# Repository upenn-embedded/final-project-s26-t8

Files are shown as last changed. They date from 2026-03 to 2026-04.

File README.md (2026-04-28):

# Final Project

**Team Number: 8**

**Team Name: Team Integr8!**

| Team Member Name | Email Address |
|---|---|
| Anjali Kalanidhi | [anjk@seas.upenn.edu](anjk@seas.upenn.edu) |
| Nevan Sujit | [tsnevan@seas.upenn.edu](tsnevan@seas.upenn.edu) |
| Sebastian William Thomann Studholme | [sthomann@seas.upenn.edu](sthomann@seas.upenn.edu) |

**GitHub Repository URL:** [https://github.com/upenn-embedded/final-project-s26-t8](https://github.com/upenn-embedded/final-project-s26-t8)

**GitHub Pages Website URL:** [https://upenn-embedded.github.io/final-project-s26-t8](https://upenn-embedded.github.io/final-project-s26-t8)

## Final Report

### 1. Video
[Demo Video](https://drive.google.com/file/d/12qTbpiO4q7P5VMjvONtVcq4hgPGpp3es/view?usp=sharing)
### 2. Images
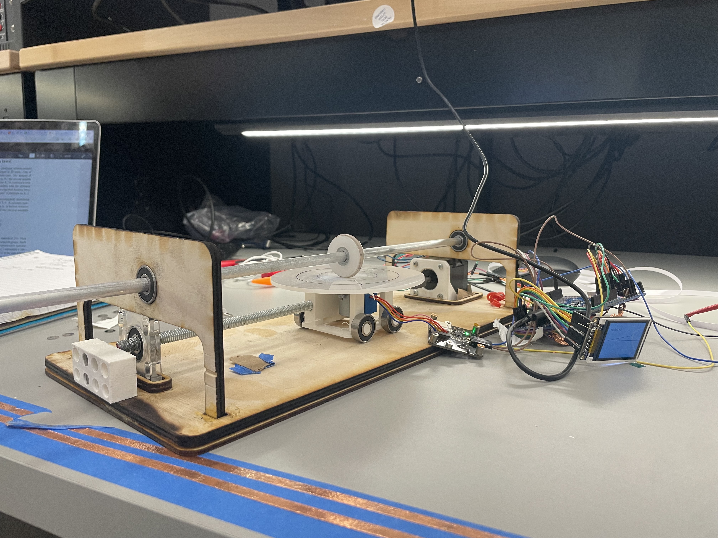
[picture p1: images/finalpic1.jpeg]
final project pictures

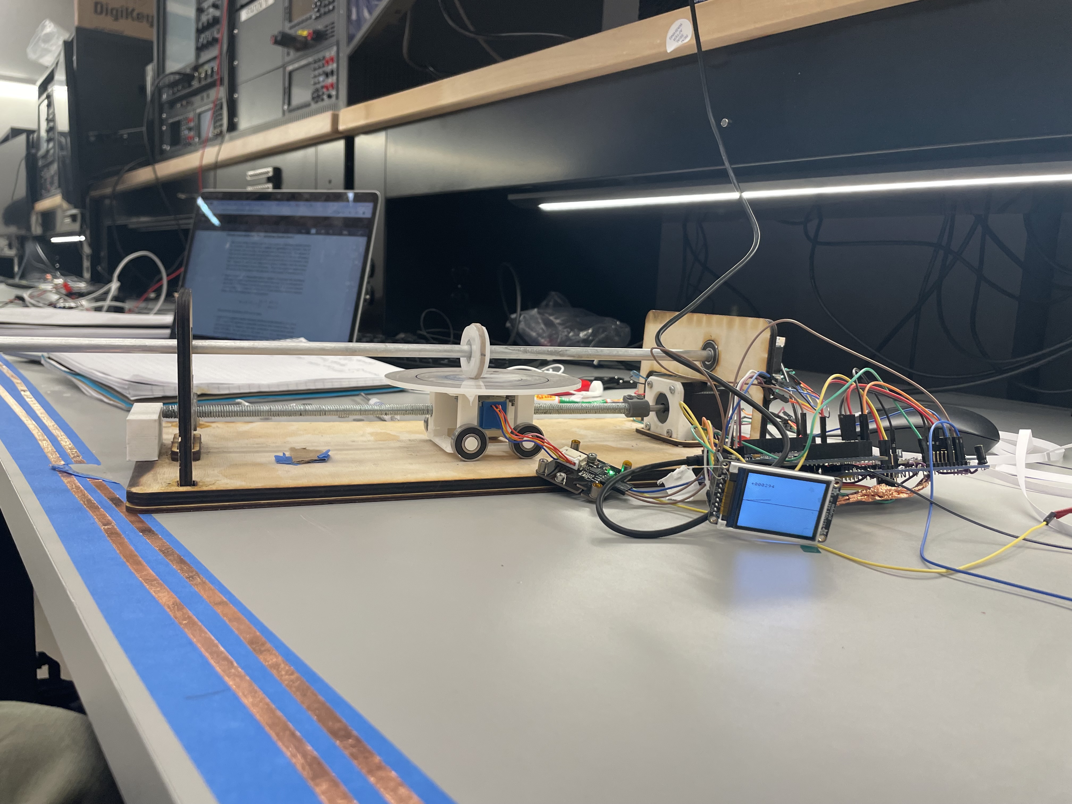
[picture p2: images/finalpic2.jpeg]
final project pictures

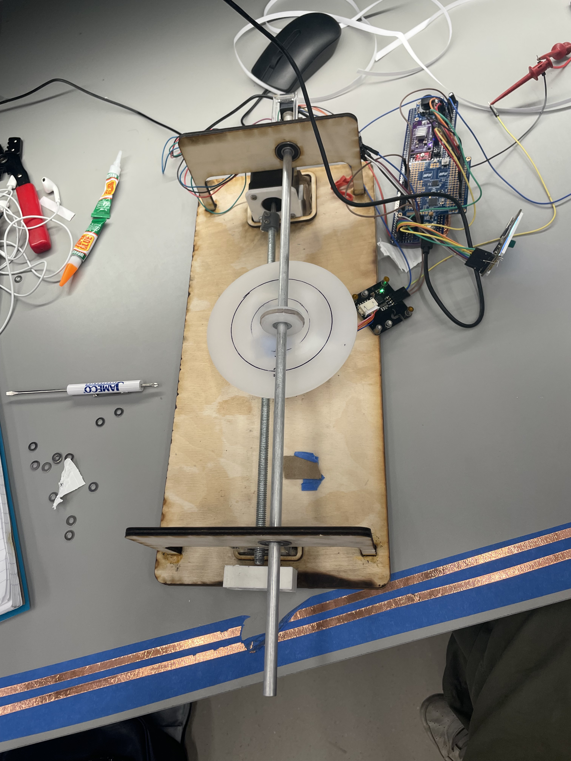
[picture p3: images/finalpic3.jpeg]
final project pictures

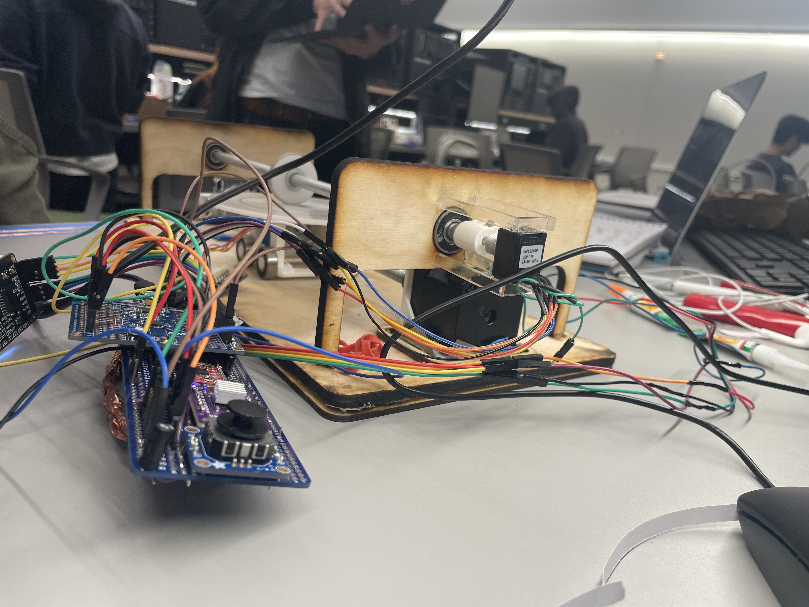
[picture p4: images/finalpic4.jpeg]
final project pictures

### 3. Results
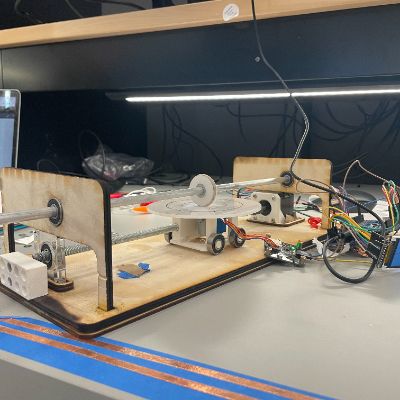
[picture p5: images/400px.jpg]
400x400 pixel picture

#### 3.1 Software Requirements Specification (SRS) Results

| ID | Description | Validation Outcome |
| --- | --- | --- |
| PWM Control | The system will generate PWM signals from the microcontroller to control motor speeds smoothly and efficiently. | Confirmed, the PWM outputs were checked via print statements and by reading an oscilloscope of the output. We had some hardware issues with this aspect, but the software worked very well. We had two different stepper motors with two different stepper motor drivers, so we had to specifically tune each code to work for each stepper motor driver, and then test and validate the PWM output coming out of each driver.  |
| Analog Input Processing | The system will read and process analog signals from the potentiometer using the onboard ADC to determine input magnitude. | We decided to use a joystick rather than a potentiometer because we felt the fact that it allowed the user to move the chassis in real time instead of simply picking a location for the chassis to end up at improved the user experience so it was easier for them to better determine which exact spot the chassis ended up at. Using the joystick also let us include variable speeds depending on how far the joystick was pushed. This system worked correctly, as we were able to check via print statements that showed us the numerical value the system was translating this input to PWM. [Joystick validation video](https://drive.google.com/file/d/1wSfRTC4DVXIuV_PTdif2x-fq1UrPfHCL/view?usp=sharing) |
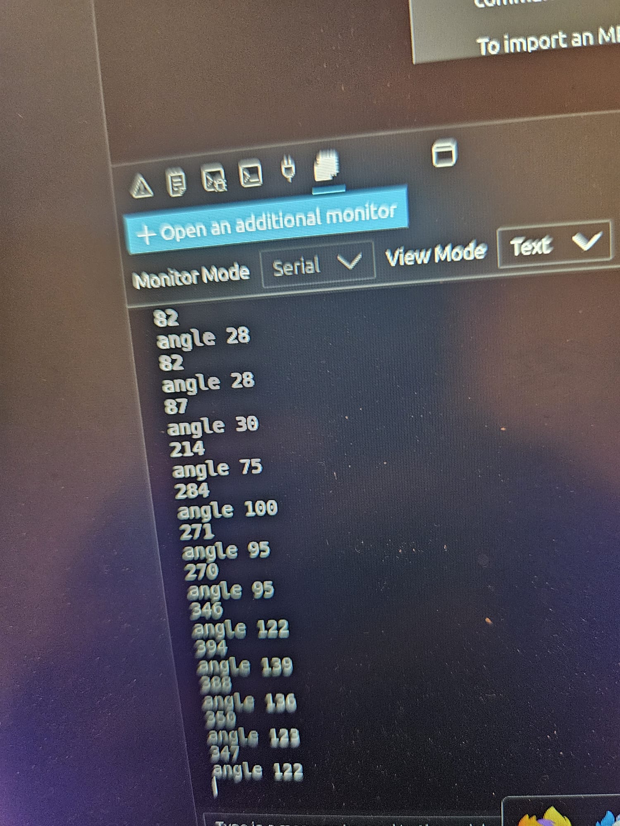
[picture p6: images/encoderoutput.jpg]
encoder validation
| Encoder Processing | The system will decode signals from the rotary encoder to track position and direction. | Works very well, we were able to confirm this is working accurately by manually measuring an angle and then using the rotary encoder and follower wheel to see if the same value is generated via print statements |
| Integration Computation | The system will keep track of rotary encoder input and sum values to calculate integral | Works well, we used print statements to see how the software sums up the positions over time, We estimate there is an error of up to 10% just by accounting for the inaccuracies of the wheel size and other mechanical limitations, but the software does its job properly. |
| Stepper Control Logic | The system will generate step and direction signals to control the stepper motor position based on the input function | We printed the out the supposed location of the stepper motor and then manually checked how far the stepper motor moved the chassis to determine if the signals were correct. This process required some tuning. |
| DC Motor Control Logic | The system will adjust DC motor speed and direction using PWM signals to maintain consistent disk rotation. | Works very well, we checked that the correct PWM signal was being generated by the software via an oscilloscope|
| Timing Control | The system will use hardware timers to maintain a fixed sampling rate for integration and motor updates. | First, we attempted to use RTOS to schedule all of the tasks needed to make this system functional. However, we ran into issues with memory space on the ATMega, so we had to switch to using ISR's instead. This ISR system works by having a hardware timer (Timer1 in CTC mode) generate an interrupt at a fixed rate of about 60 Hz, and this ISR acts as the high-priority control loop. Inside the ISR, the program reads the encoder, updates the running integral, samples the ADC, and adjusts the motor PWM and direction, ensuring these operations execute consistently. Meanwhile, the main loop runs independently as a low-priority task, handling slower operations like updating the LCD display and formatting output, even though it includes blocking delays. We ensured that this system worked by looking at an oscilloscope to see which task was happening when periodically.  |
| Display Software | The system will update the LCD via I2C to display input values, output values, and system status in real time. | Works well, we were simply able to validate this system works by checking the screen and ensuring that what we wanted to show up on the screen was actually showing up. Earlier on, we ran into some issues where the screen was not updating properly, or would turn blank after a certain amount of time, but we realized this was because the system did not have enough time to properly initialize, so by adding delays into our code, we were able to fix this issue. |

#### 3.2 Hardware Requirements Specification (HRS) Results

| ID | Description | Validation Outcome |
| --- | --- | --- |
| Power Supply Hardware | The system should include a 9 V battery and a buck converter to provide a stable 5 V supply to all electronic components. | We were unable to meet this requirement due to changes in the power requirments for the system. We initially thought our stepper motors would require 9V, but the more heavy Nema 17 motor required 24V. As a result, we were not able to order a 24V power supply in time for the demo, so we used the voltage supply for all voltages needed |
| User Input Hardware | The system should include a slider potentiometer that allows the user to manually define the input to the integrator. |Works well, we were able to check what the input is by measuring the distance the chassis moves. Our input is through a joystick instead of potentiometer, and the input signal is also relative to the maximum y values we set (the range being -2 to 2 for the final product of this project), so there were some limitations with how accurate this input could be based on what function the user actually wishes to input, but that is more of a matter of mechanical limitations rather than hardware issues. |
| Disk Rotation | There will be a DC motor-driven rotating plate mechanism that rotates at constant speed to represent time | The disk rotation was quite easy to accomplish and validate, as we were able to use an oscilloscope to see the PWM signal, and then manually count how long it takes the disk to complete a rotation to ensure that the motor driver and motor were working properly. We ended up changing this motor from a DC motor driver to a stepper motor, as that allowed us to rotate the plate at a constant speed more easily within the software stack |
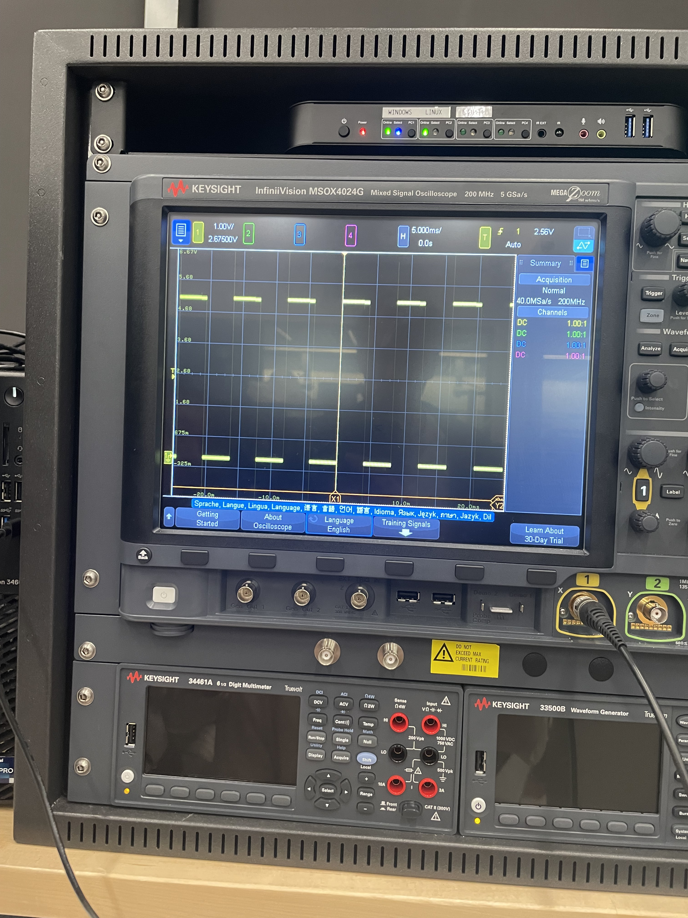
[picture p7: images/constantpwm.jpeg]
constant pwm
| DC Motor Driver | The system will include a motor driver to control the speed of the DC motor using PWM signals. | We had a lot of issues with this motor driver, as the driver fried twice. The first time, we swapped out the driver and the second time, we unsoldered and resoldered a new chip onto the motor driver, fixing these issues. We think this issue was caused by abruptly giving the motor driver power and turning it off when testing. Similar to the requirement above, we were able to validate that the output of this motor driver was correct with an oscilloscope, and this aspect of the project worked very well. Below is the PWM output for the constant plate stepper motor:  |
| Stepper motor function input | There will be a stepper motor-driven mechanism that adjusts the location of the chassis based on the input function | For the most part, this system works quite well. However, in the beginning we ran into many issues with the stepper motor stalling when we gave it power, and we spent a lot of time debugging that issue. Eventually, we realized it was due in part to torque issues caused by the clamp connecting the motor to the rod it was supposed to be turning, so we loosened the rod and attached it with glue (it could be unglued as well after use!). |
| Stepper Motor Driver | The system will include a stepper motor driver to provide precise position control via step and direction signals from the microcontroller. | We had some issues with this stepper motor beause we realized the current limit for the motor driver was set too low, causing the Nema-17 motor to stall. By increasing the potentiometer on the driver, we were able to fix this problem. This system worked pretty well, though we estimated there was likely a 10% error due to mechanical issues that happened within the system after the stepper motor driver supplied the PWM signal to the motor. We checked that the correct signal was being supplied via an oscilloscope [Stepper motor driver validation](https://drive.google.com/file/d/1TqjuBm9TQkSATUtn5irRsQ1cWkJYZEgd/view?usp=sharing) |
| Output Shaft Sensing | The system will include a rotary encoder mechanically coupled to the output shaft so that shaft rotation can be measured electronically. | Using the rotary encoder worked very well, especially once we were able to solder the pins properly. We had a few mechanical issues with placing the rotary encoder so it did not move, but overall through testing and mechanical tuning we were able to ensure this process works well through print statements. |
| Display Hardware | The system will have an LCD display connected through I2C to present system information to the user during operation. | We were able to get this system working well so that it displays the integral function as well as the value of the integral. We originally had some overflow issues with the display, causing it to blank out, but by switching from an RTOS system to one dirven by ISR's and adding in proper delays for startup, we were able to fix this problem. |

### 4. Conclusion
Overall, we found this project to be immensly fulfilling and each felt that our we gained very valuable skills not only in embeded C, but in learning how to plan and put a whole project together, learning which parts to pick and what to account for when picking parts, and how to CAD, laser cut, and understand how to integrate software, electrical, and mechanical parts together to make a complete project. 

Some important things we learned about were knowing which software techniques to use when (RTOS may have been better at scheduling, but the memory limitations of the ATMega showed us that using ISR's was the better option). We also worked on many different parts of the code at once, and then had to integrate them all together, which allowed different members of the team to always have something to do, but led to some changes having to be made during software integration to account for the fact that different people writing code may affect the efficiency of the system. We also got good at learning how to diagnose if a problem was due to software, electrical, or mechanical components, like when our Nema 17 motor was stalling (a mix of electrical and mechanical) or when the LCD screen was not displaying properly (software). A big unexpected challenge for us was putting all the mechanical components together. We understood that this project was very mechanical-heavy, but underestimated how many clamps and chassis' would break, had a lot of trouble figuring out tolerances (tolerances for laser cutting with wood vs acrylic vs 3D printing led to a **lot** of trial and error), and didn't really account for the time it takes to lasercut/print. As a result, on the morning of our demo, the threading in our chassis that allows the Nema-17 to move the plate left and right wore down, and we were scrambling to print a new one for our demo. Overall, we felt that we met pretty much all of our software/hardware requirements, but the mechanical aspects of our project were what was holding us back from making it even more complete. Our project is a great prototype, but next time, designing with mechanical integration in mind earlier could help us a lot in minimizing error. Our next steps for this project would be to redesign our actual frame so it fits together better and to consolidate our power supplies with a buck converter so we can power the entire system with a single 24V power supply.

## References
We first learned about the mechanical integrator from a Youtube video titled [The Mechanical Integrator - a machine that does calculus](https://www.youtube.com/watch?v=s-y_lnzWQjk) by Jack Monaco. We wanted to try and build this project for ourselves, adding complexity with the LCD screen as well as user input. We emailed the author of this video to ask him for the CAD model of his design to use as a basis for ours, but found that his design was pretty underdeveloped/incomplete. Instead, we used his design as a basis to create our CAD model.

## Final Project Proposal

### 1. Abstract
A mechanical integrator is a device that physically computes the integral of a function by converting a changing input into accumulated motion over time. Historically, mechanisms like these were used in early analog computers to solve math problems before modern digital computers were available. In this project, we are building a microcontroller-assisted mechanical integrator that demonstrates this concept in an interactive way. A slider potentiometer allows the user to control a time-varying input value, which is read by an ATmega328P microcontroller. The system drives a motor that changes speed as an analog to the function value over time and the mechanical integrator uses the motor encodings to calculate the accumulated distance travelled over time, which is an analog to an integral. The microcontroller will output the behavior of the input and the resulting integral on a small LED display and on the serial plotter. 

### 2. Motivation
We are building our mechanical integrator to create a more computation-efficient way to solve integrals, particularly because the ATMega328P is not well-suited for computing complex mathematical problems. This project is interesting because we are building a mechanical integrator, a device that was historically used to calculate complex integrals, but updating it with the modern firmware capabilities of the ATMega to show that analog based technologies still have their merits.

### 3. System Block Diagram
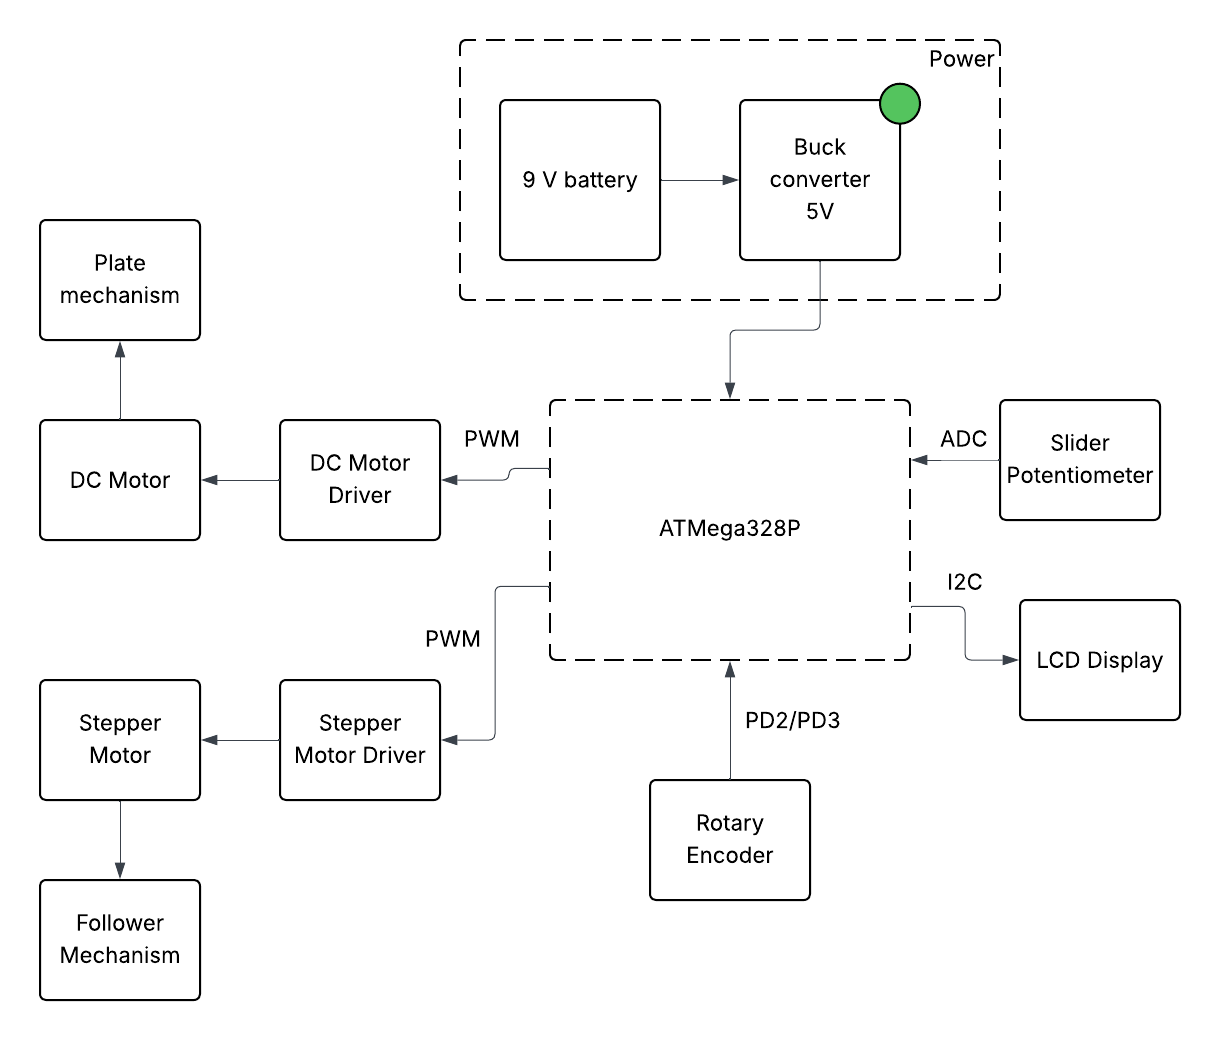
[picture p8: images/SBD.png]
System Block Diagram

### 4. Design Sketches
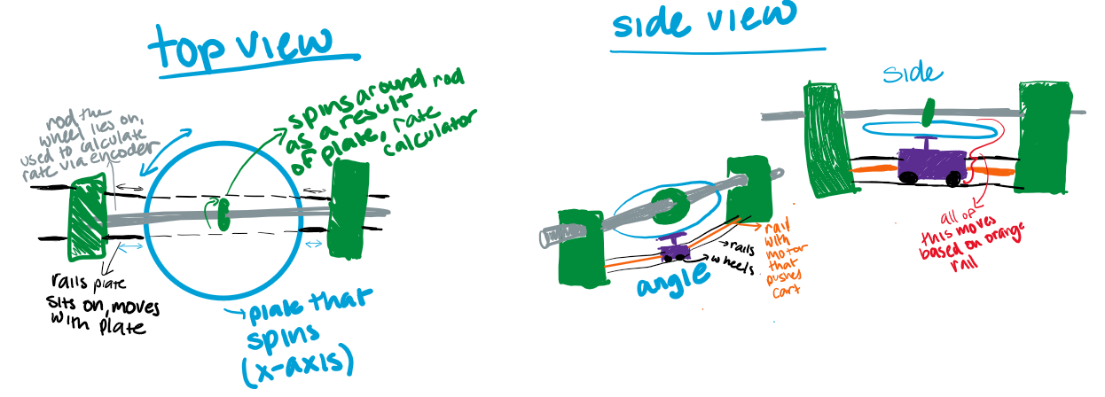
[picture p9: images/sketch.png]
Sketch

### 5. Software Requirements Specification (SRS)

**5.1 Definitions, Abbreviations**

Here, you will define any special terms, acronyms, or abbreviations you plan to use for hardware

**5.2 Functionality**

| ID | Description |
| --- | --- |
| PWM Control | The system will generate PWM signals from the microcontroller to control motor speeds smoothly and efficiently. |
| Analog Input Processing | The system will read and process analog signals from the potentiometer using the onboard ADC to determine input magnitude. |
| Encoder Processing | The system will decode signals from the rotary encoder to track position and direction. |
| Integration Computation | The system will keep track of rotary encoder input and sum values to calculate integral |
| Stepper Control Logic | The system will generate step and direction signals to control the stepper motor position based on the input function |
| DC Motor Control Logic | The system will adjust DC motor speed and direction using PWM signals to maintain consistent disk rotation. |
| Timing Control | The system will use hardware timers to maintain a fixed sampling rate for integration and motor updates. |
| Display Software | The system will update the LCD via I2C to display input values, output values, and system status in real time. |

### 6. Hardware Requirements Specification (HRS)

**6.1 Definitions, Abbreviations**

Here, you will define any special terms, acronyms, or abbreviations you plan to use for hardware
Plate: The bottom, flat, circular disk that is rotated by a motor to represent the x-axis.
Follower: the small wheel attached to a rod that spins as a result of the plate rotation

**6.2 Functionality**

| ID | Description |
| --- | --- |
| Power Supply Hardware | The system should include a 9 V battery and a buck converter to provide a stable 5 V supply to all electronic components. |
| User Input Hardware | The system should include a slider potentiometer that allows the user to manually define the input to the integrator. |
| Disk Rotation | There will be a DC motor-driven rotating plate mechanism that rotates at constant speed to represent time |
| DC Motor Driver | The system will include a motor driver to control the speed of the DC motor using PWM signals. |
| Stepper motor function input | There will be a stepper motor-driven mechanism that adjusts the location of the chassis based on the input function |
| Stepper Motor Driver | The system will include a stepper motor driver to provide precise position control via step and direction signals from the microcontroller. |
| Output Shaft Sensing | The system will include a rotary encoder mechanically coupled to the output shaft so that shaft rotation can be measured electronically. |
| Display Hardware | The system will have an LCD display connected through I2C to present system information to the user during operation. |

### 7. Bill of Materials (BOM)
A 10k slider potentiometer will serve as the primary input as it will be used as the analog for function value over time. The potentiometer will be connected to an ADC pin on the microcontroller so that the system can read the input value.

The mechanical integrator requires two motors. A DC gear motor will rotate the time disk, providing the constant motion needed for the integration process. This motor will be controlled using a motor driver, which allows the microcontroller to regulate motor speed using PWM signals. A stepper motor will be used to control the position of the follower mechanism. A stepper motor is needed here as we need precise position control and it will be driven using an EasyDriver stepper motor driver.

To measure the output of the integrator, a rotary encoder will be attached to the output shaft. The encoder will generate pulses that the microcontroller can count using interrupt pins to determine how much the shaft has rotated.

Finally, an LCD display will be used to display the integral value. The display will communicate with the microcontroller using the I2C interface and will show information such as the input value and the integrated output.

[BOM](https://docs.google.com/spreadsheets/d/1b2L2CsoX9tYtY7pSSJdgno0QYMjl8iTiAHsGNdwpyRs/edit?usp=sharing)

### 8. Final Demo Goals
On demo day, the device will be demonstrated on tabletop. A user will control the input function using the slider potentiometer, which changes the motor speed over time. As the slider is moved, the mechanical system will compute the integral through its physical motion, while the microcontroller reads and visualizes the output integral on an LED display.

During the demonstration, several simple input patterns representing basic functions will be shown, such as holding the slider at a constant value (y=c), changing it linearly over time (y=mx), and sinusoidal functions. These examples will illustrate how the output accumulates and how the integral changes based on the input. The main constraints for the demo are ensuring that the mechanical components are properly aligned and calibrated.

### 9. Sprint Planning

| Milestone  | Functionality Achieved | Distribution of Work |
| --- | --- | --- |
| Sprint #1  | Build the entire project on CAD. Since this project requires a fair amount of laser cutting + 3D printing, we want to make sure that we design all those parts before we design anything physically. Not only should the entire design, including the manufactured parts and electrical components be in our CAD design, but we also want to create simulations in our design for how the mechanisms should move.  | Anjali CAD's the plate & things it is connected to, Nevan CAD's the follower and things it is connected to, Sebastian CAD's all integration |
| Sprint #2  | Following this our second milestone will be to both print and assemble the manufactured parts with the electrical components, and then program the MCU to take in the potentiometer input and output the correct PWM signals and take the motor’s encodings to calculate the integral. With these two milestones, we will have essentially finished building our project. | Anjali handles printing of parts and mechanical side of things, Sebastian works on software, Nevan works on electronics. Everyone is working together to integrate, so tasks are not as clear cut |
| MVP Demo | Potentiometer input leads to function displayed through serial monitor, integral output, as well as LCD showing the integral numerical value. | Anjali works further on mechanical/software integration, Sebastian and Nevan finish coding. Most of this week will be spent tuning device and making sure it works well. |
| Final Demo | if time permits we want to build a way for the user to draw rather than use a potentiometer to create their function. The user would draw their desired function that they want to integrate on a display and then this drawing gets converted to a list of numbers that the MCU can then read to control the PWM signal to input into the motor. The output could then also be displayed in the serial as the distance travelled by the motor over time. | Sebastian CAD's mechanical components, Anjali and Nevan work on software/electrical updates to make new features work. |

**This is the end of the Project Proposal section. The remaining sections will be filled out based on the milestone schedule.**

## Sprint Review #1

### Last week's progress
We have CAD'd most of the model for the project and ordered all the components we need. We finalized which components we wanted to go with, including picking which motors to use and deciding which components in Detkin we can use and which components we want to order. We have finalized the CAD design for the wheel and for the connectors between the frame and the rods. We have begun laser cutting and are planning on finishing assembly physically integrate our electronic components into the design next week. We still need to figure out how to add wheels to the chassis that the plate spins on and how to connect the rotary encoder to the follower wheel and shaftf, so those will be mechanical challenges we need to figure out next week.
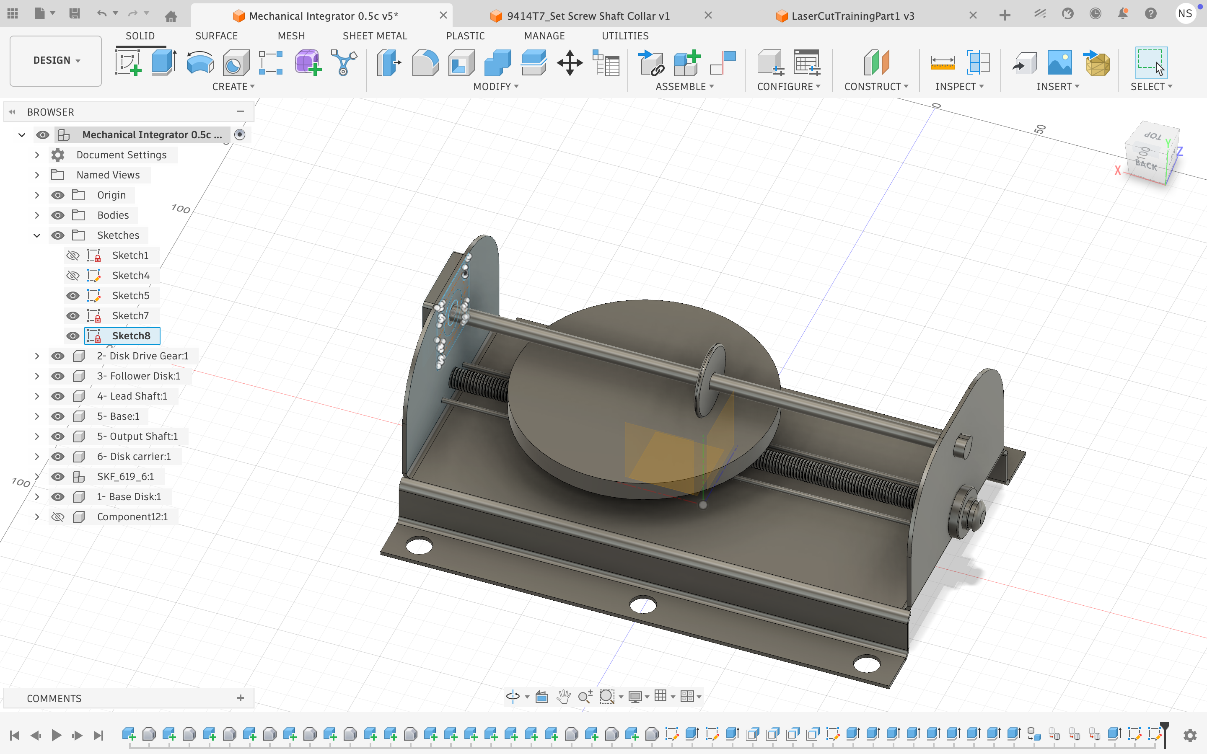
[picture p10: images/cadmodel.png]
cad model

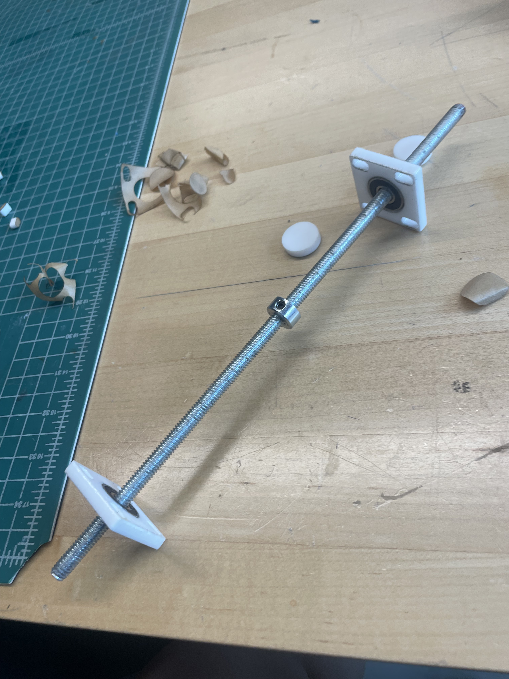
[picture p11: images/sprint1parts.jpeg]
parts we cut

### Current state of project
We have a pretty solid foundation for this project. We understand how it works mechanically, which parts should be connected to one another, and how we want to integrate electronics. We have all parts purchsed, and at this point we just need to focus on finishing the mechanical parts and assembly as soon as possible so we can focus on hardware.
### Next week's plan
Finishing printing and assembly, create a plan for how we are physically going to wire up our components, and create system diagrams for our code so we can integrate everything completely the week after.
| Assignee | Task | Estimated time | Finished when... |
| ---| -----|--- | --- |
| Nevan  | CAD and print the chassis | Two hours | The chassis is printed |
| Sebastian  | Connector between rotary encoder and follower shaft wheel | Two hours | Connector is printed and glued to rotary encoder and shaft |
| Anjali | Connect follower wheel to shaft to bearings to rotary encoder | 1 hour | Entire top piece is connected |
| Nevan | CAD and print base | Two hours | Base is printed |
| Anjali | CAD and print wheels | Two hours | Wheels are printed and connected to chassis as well as track |
| Sebastian | Final assembly | Two hours | Connect all pieces together, motors are placed in correct location |
## Sprint Review #2

### Last week's progress
We completely finished CADing and most of our parts are printed. We had to alter tolerances because we made some of them too tight, so we are currently just waiting on those last parts to print. Most of our electronics have come in as well so we have begun to write code as well as assemble. We are splitting each of the components into separate code segments and then planning on integrating all the code together. The code for the follower wheel encoder, which actually calculates the integral, is complete. 
output from encoder
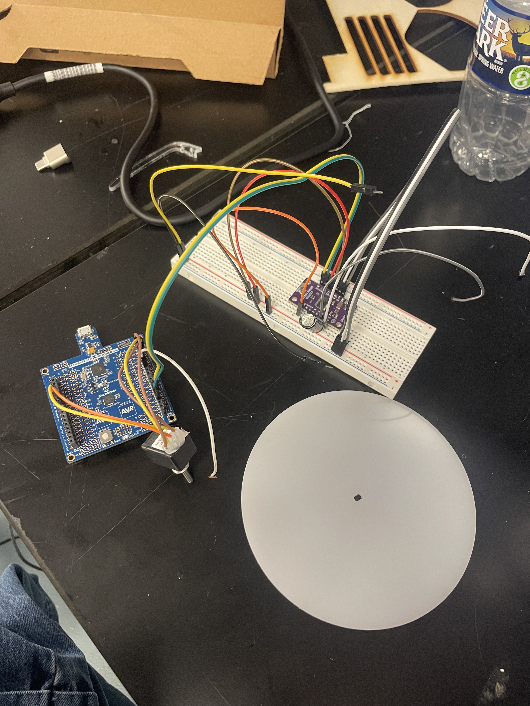
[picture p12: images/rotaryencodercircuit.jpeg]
circuit with rotary encoder

### Current state of project
We have code for the rotary encoder that tells you the correct integral value, and most of the components assembled together, we just need to add them to the frame.
### Next week's plan
Finishing coding is top priority, then working on assembly. There are lag times in getting our mechanical parts finished, but since we have the motors and drivers we need, we can work on writing code in the meantime to make integration go smoother. Because the mechanical aspect of this project is taking longer than expected, we are focusing on getting the integral to work with a manual function input, and then will add user input the following week.
| Assignee | Task | Estimated time | Finished when... |
| ---| -----|--- | --- |
| Nevan  | print the frame | one hour | The frame is printed/ made sure all componenets are correct sizes/fit |
| Sebastian  | assemble the frame | two hours | mechanical frame is fully complete with all separate components |
| Anjali | integrate electronics  | 2 hour | all electronics are in the frame |
| Nevan | code the big stepper motor/y axis | five hours | the rod moves in tandem with the y axis of a function |
| Anjali | code the time/constant plate, integrate all code together | five hours | all code is complete |
| Sebastian | final integration | five hours | Connect all pieces together, motors are placed in correct location, fully integrated together |
| Nevan | Code LCD Screen output | two hours | LCD properly displays what integral value we want it to |
## MVP Demo
[Slide deck](https://docs.google.com/presentation/d/1c26fR2l8V-HrHxDpfWXI8LoWvZEP7CJ0bPEYAke9Whs/edit?usp=sharing)

System block diagram:
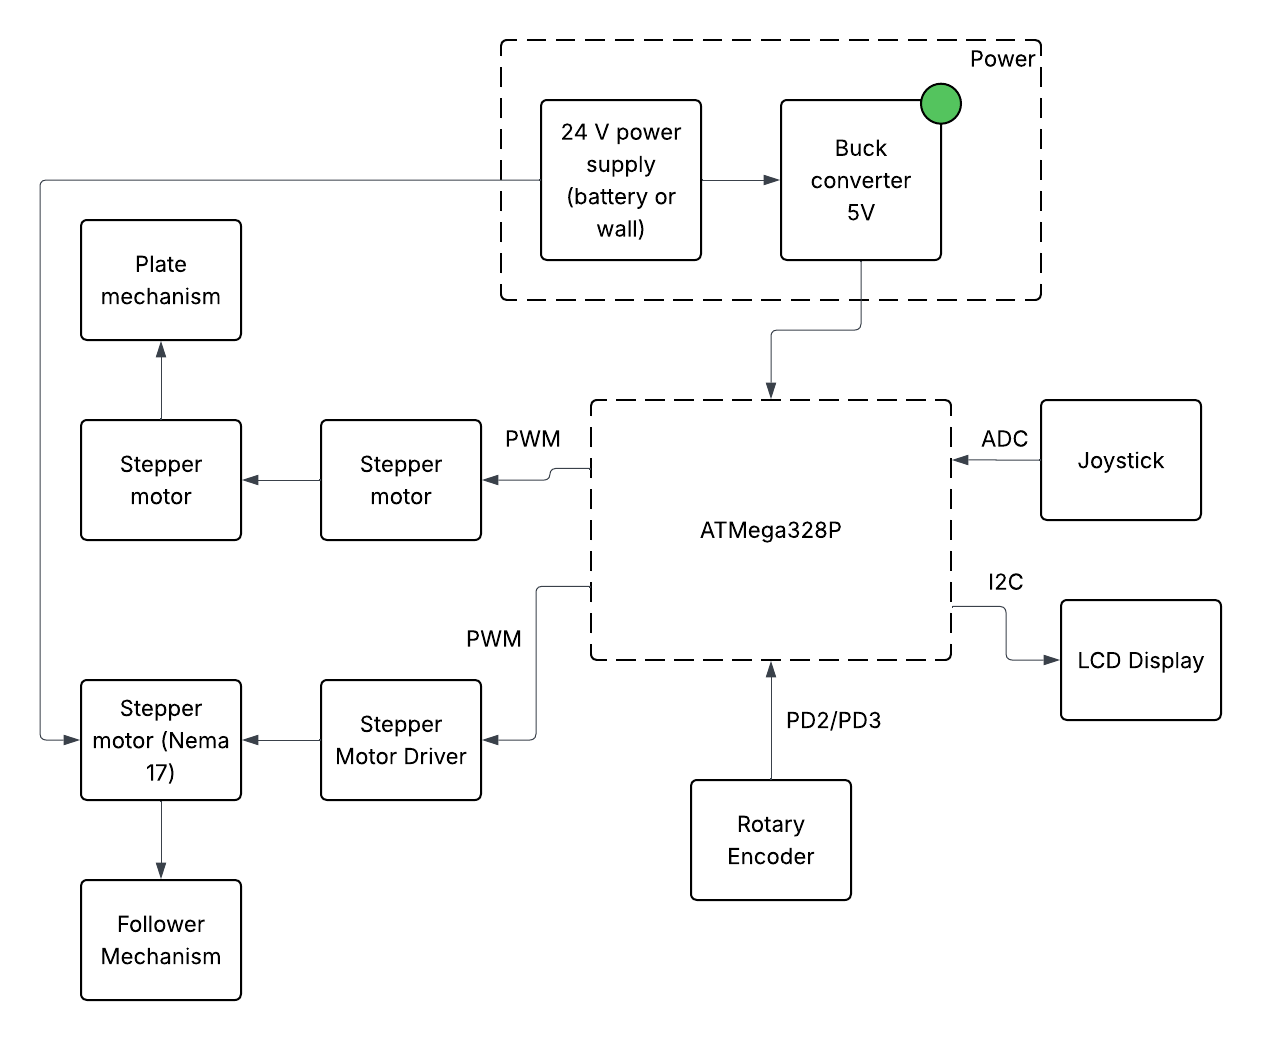
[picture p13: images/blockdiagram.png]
System block diagram


Hardware explanation:
The hardware system is organized around the ATmega328P microcontroller, which serves as the central controller coordinating power, sensing, and actuation. A 24 V power supply provides the primary energy source, which is stepped down to 5 V using a buck converter to safely power the microcontroller and low-voltage peripherals. User input is provided through a joystick connected to an ADC pin. The ATMega processes this input and turns it into PWM outputs for the motors. One stepper motor (turning the plate) establishes the time base by driving the plate mechanism, while another stepper motors (the heavy duty NEMA 17) is used to represent the y axis of the function input. This movement turns the follower wheel, which turns the rotary encoder connected to digital pins (PD2/PD3) which read the angle position. The ATMega then processes this data and sums up the overall change in angle to find the total integral. An LCD display communicates with the microcontroller over I2C, enabling real-time visualization of the integral as well as its value. The system operates in a closed-loop style at the user level: the user sets an input via the potentiometer or joystick, the microcontroller processes this input and generates appropriate control signals, the motors actuate the mechanical system, and the resulting motion is observed through the encoder feedback and displayed on the LCD.

Firmware implementation:
The firmware is structured into modular components that separately handle sensing, user interaction, and motor control while remaining tightly coordinated through the main control loop. One module manages the rotary encoder and LCD output, where interrupt-driven inputs from the encoder (on PD2/PD3) are used to track position or system output in real time, and this information is formatted and transmitted over I2C to the display for user feedback. A second module controls the NEMA 17 stepper motor responsible for the y-axis (input function), generating precise step and direction signals to map the user-defined input—set via the potentiometer or joystick—into accurate vertical motion. The third module governs the stepper motor driving the plate mechanism, which acts as the x-axis (time base) by running at a constant, calibrated speed to ensure a uniform progression of time. Together, these modules create a synchronized firmware architecture where the time axis advances steadily, the input axis responds dynamically to user control, and the system state is continuously measured and displayed, effectively implementing the mechanical integration behavior.

Software Requirements Specifications:
The software is designed to integrate sensing, computation, and actuation into a single cohesive system. Analog input processing is implemented thorugh the joystick, allowing user-defined inputs to be continuously sampled. Rotary encoder processing is tightly coupled with the integration computation, enabling real-time calculation of the system’s output within the same execution flow. While the integration logic is functional and produces correct mathematical behavior, further tuning of variables is required to improve accuracy and stability. During development, stack overflow issues were encountered, indicating memory constraints that required optimization of function usage and data handling. Stepper motor control for the input axis and time axis are both operational, though additional tuning is needed—particularly for incorporating encoder feedback to correct accumulated positional errors over time.

From a timing perspective, a structured scheduling approach through RTOS has been implemented to reliably sequence encoder reading, integration computation, and LCD updates, ensuring consistent real-time performance. However, this timing framework still needs to be extended to both stepper motors. The display system is complete, providing clear real-time feedback of system state, including input and output values. Overall, the software is functionally complete but requires further calibration and optimization, as well as full integration of all systems through RTOS.

Hardware Requirement Specifications:
The hardware implementation centers on the ATmega MCU. Power is currently supplied through multiple working sources, so distribution architecture still needs to be consolidated. User input is provided via a joystick that feeds analog signals into the MCU, where the ADC reliably converts them into digital values for processing. The rotary encoder is functioning well and provides consistent, accurate measurements, while the disk rotation mechanism for the time axis is also operating as expected. The display hardware and stepper motor driver are both stable and performing reliably within the system.

On the actuation side, stepper motor drivers are generally functional but require further tuning, particularly for the NEMA 17 motor, which is experiencing jitter and lag. These issues are mostly caused by mechanical factors such as friction, misalignment, or load inconsistencies in the mechanism. Overall, while the core hardware components are working, final performance depends on improving both driver tuning and mechanical integration to reduce lag and ensure consistent motion.

Risk mitigation:
To mitigate the risk of high voltage damaging components or overheating motors, hardware safeguards such as current limiting, proper driver configuration, and protective circuitry (e.g., fuses or thermal shutdown features) are implemented to prevent excessive power draw. Mechanical failures are addressed by reinforcing all structural components using secure fasteners like screws instead of adhesives, ensuring greater durability and stability under load. Together, these measures improve both electrical safety and mechanical reliability of the system.

Next steps:
The next steps focus on fully integrating the mechanical and control subsystems into a single cohesive system, ensuring that the firmware and hardware operate seamlessly together. Mechanically, the device will be assembled and reinforced, while the power system will be standardized to a single wall supply for simplicity and reliability. Additionally, debugging efforts will target stepper motor jittering to improve motion smoothness and overall system performance.

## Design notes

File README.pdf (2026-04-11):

README.md | 2026-04-11

# Final Project

Team Number: 8

Team Name: Integr8

Team Member Name | Email Address
Anjali Kalanidhi | anjk@seas.upenn.edu
Nevan Sujit | tsnevan@seas.upenn.edu

Sebastian William Thomann Studholme sthomann@seas.upenn.edu

GitHub Repository URL: https://github.com/upenn-embedded/final-project-s26-t8

GitHub Pages Website URL: [for final submission]*

## Final Project Proposal

1. Abstract

A mechanical integrator is a device that physically computes the integral of a function by converting a changing input into accumulated motion over time. Historically, mechanisms like these were used in early analog computers to solve math problems before modern digital computers were available. In this project, we are building a microcontroller-assisted mechanical integrator that demonstrates this concept in an interactive way. A slider potentiometer allows the user to control a time-varying input value, which is read by an ATmega328P microcontroller. The system drives a motor that changes speed as an analog to the function value over time and the mechanical integrator uses the motor encodings to calculate the accumulated distance travelled over time, which is an analog to an integral. The microcontroller will output the behavior of the input and the resulting integral on a small LED display and on the serial plotter.
2. Motivation

We are building our mechanical integrator to create a more computation-efficient way to solve integrals, particularly because the ATMega328P is not well-suited for computing complex mathematical problems. This project is interesting because we are building a mechanical integrator, a device that was historically used to calculate complex integrals, but updating it with the modern firmware capabilities of the ATMega to show that analog based technologies still have their merits.
3. System Block Diagram

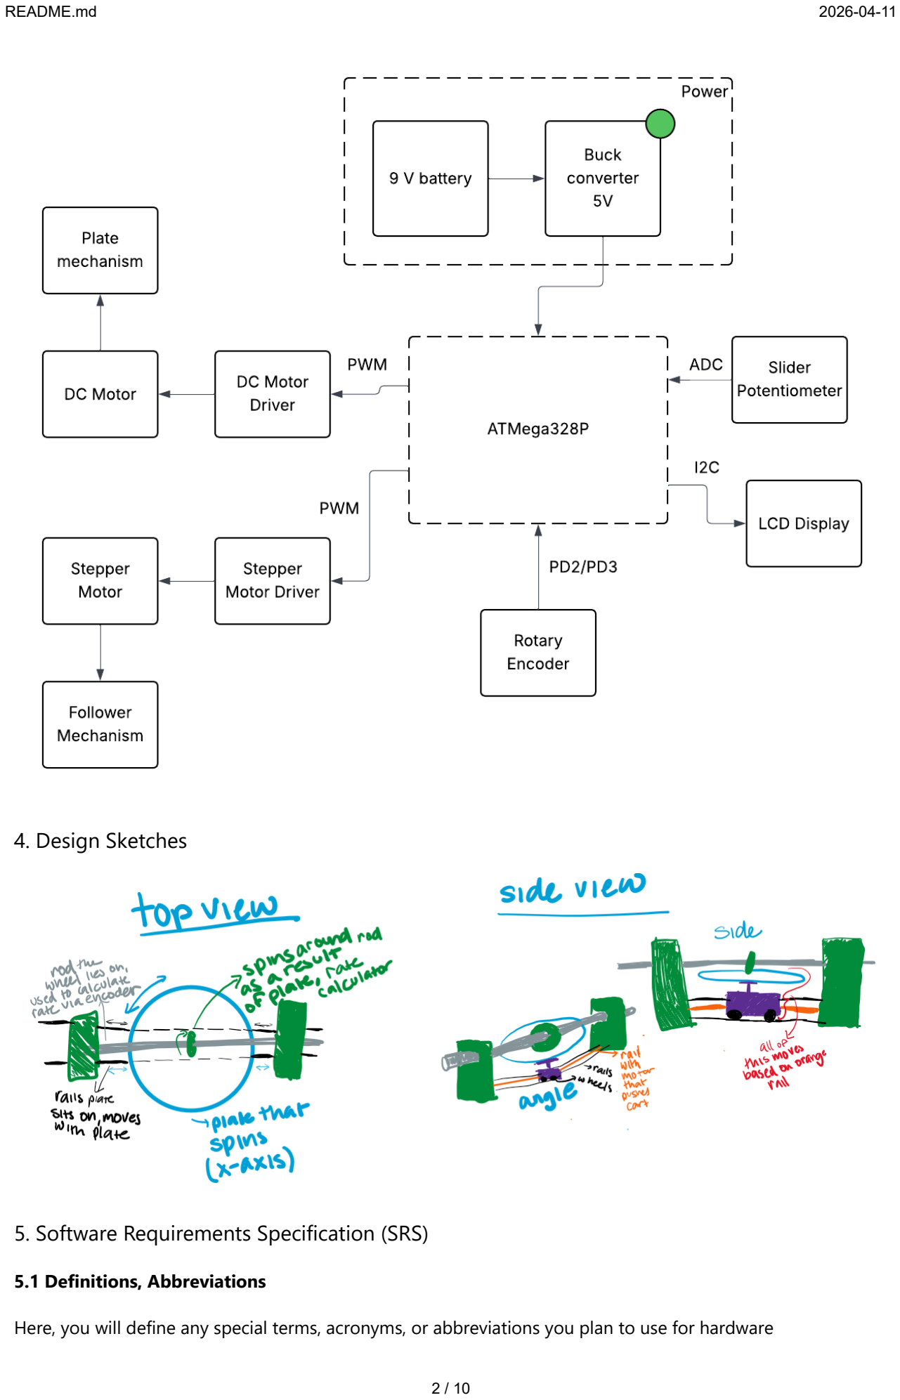
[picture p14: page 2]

4. Design Sketches
5. Software Requirements Specification (SRS)

### 5.1 Definitions, Abbreviations

Here, you will define any special terms, acronyms, or abbreviations you plan to use for hardware

### 5.2 Functionality

ID | Description
Analog Input Sampling | The IMU 3-axis acceleration will be measured with 16-bit depth every 100 milliseconds +/-10 milliseconds

Constant
Disk Motor Control | The software shall drive the disk motor at a constant speed using PWM control.

Follower
position

The software should drive the stepper motor to move the follower mechanism according to the input value from the slider potentiometer. We can test this by setting several known slider positions and checking that the follower moves to the expected corresponding positions.

Output
measurement

The software should read pulses from the rotary encoder using interrupts in order to track the output shaft rotation in real time. We’ll test this by rotating the output shaft by a known amount and checking that the encoder count changes by the expected amount.

LCD Display

The software should update the LCD display and serial plotter in real time to show the current input value and the accumulated output of the integrator.

6. Hardware Requirements Specification (HRS)

### 6.1 Definitions, Abbreviations

Here, you will define any special terms, acronyms, or abbreviations you plan to use for hardware Plate: The bottom, flat, circular disk that is rotated by a motor to represent the x-axis. Follower: the small wheel attached to a rod that spins as a result of the plate rotation

### 6.2 Functionality

ID | Description
User Input Hardware | The system should include a slider potentiometer that allows the user to manually define the input to the integrator.
Disk rotation | There will be a motor-driven rotating disk that provides the time base for the mechanical integrator.
Follower position movement | There will be a motorized follower-position mechanism that adjusts the follower location based on the user input. We will test this by making the mechanism move to multiple positions and verifying it moves to those correct positions.
Output Shaft Sensing | The system will include a rotary encoder mechanically coupled to the output shaft so that shaft rotation can be measured electronically.
Display Hardware | The system will have an LCD display connected through I2C to present system information to the user during operation.
7. Bill of Materials (BOM)

A 10k slider potentiometer will serve as the primary input as it will be used as the analog for function value over time. The potentiometer will be connected to an ADC pin on the microcontroller so that the system can read the input value.

The mechanical integrator requires two motors. A DC gear motor will rotate the time disk, providing the constant motion needed for the integration process. This motor will be controlled using a motor driver, which allows the microcontroller to regulate motor speed using PWM signals. A stepper motor will be used to control the position of the follower mechanism. A stepper motor is needed here as we need precise position control and it will be driven using an EasyDriver stepper motor driver.

To measure the output of the integrator, a rotary encoder will be attached to the output shaft. The encoder will generate pulses that the microcontroller can count using interrupt pins to determine how much the shaft has rotated.

Finally, an LCD display will be used to display the integral value. The display will communicate with the microcontroller using the I2C interface and will show information such as the input value and the integrated output.

BOM (https://docs.google.com/spreadsheets/d/1b2L2CsoX9tYtY7pSSJdgno0QYMjl8iTiAHsGNdwpyRs/edit?usp=sharing)
8. Final Demo Goals

On demo day, the device will be demonstrated on tabletop. A user will control the input function using the slider potentiometer, which changes the motor speed over time. As the slider is moved, the mechanical system will compute the integral through its physical motion, while the microcontroller reads and visualizes the output integral on an LED display.

During the demonstration, several simple input patterns representing basic functions will be shown, such as holding the slider at a constant value (y=c), changing it linearly over time (y=mx), and sinusoidal functions. These examples will illustrate how the output accumulates and how the integral changes based on the input. The main constraints for the demo are ensuring that the mechanical components are properly aligned and calibrated.
9. Sprint Planning
Milestone Functionality Achieved | Distribution of Work

Sprint #1

Build the entire project on CAD. Since this project requires a fair amount of laser cutting + 3D printing, we want to make sure that we design all those parts before we design anything physically. Not only should the entire design, including the manufactured parts and electrical components be in our CAD design, but we also want to create simulations in our design for how the mechanisms should move.

Anjali CAD's the plate &
things it is connected to, Nevan CAD's the follower
and things it is connected to, Sebastian CAD's all
integration

Milestone Functionality Achieved | Distribution of Work

Sprint #2

Following this our second milestone will be to both print and assemble the manufactured parts with the electrical components, and then program the MCU to take in the potentiometer input and output the correct PWM signals and take the motor’s encodings to calculate the integral. With these two milestones, we will have essentially finished building our project.

Anjali handles printing of parts and mechanical side
of things, Sebastian works on software, Nevan works
on electronics. Everyone
is working together to
integrate, so tasks are not as clear cut

MVP
Demo

Potentiometer input leads to function displayed through serial monitor, integral output, as well as LCD showing the integral numerical value.

Anjali works further on
mechanical/software
integration, Sebastian and Nevan finish coding. Most
of this week will be spent tuning device and making
sure it works well.

Final
Demo

if time permits we want to build a way for the user to draw rather than use a potentiometer to create their function. The user would draw their desired function that they want to integrate on a display and then this drawing gets converted to a list of numbers that the MCU can then read to control the PWM signal to input into the motor. The output could then also be displayed in the serial as the distance travelled by the motor over time.

Sebastian CAD's
mechanical components,
Anjali and Nevan work on
software/electrical
updates to make new
features work.

This is the end of the Project Proposal section. The remaining sections will be filled out based on the milestone schedule.

## Sprint Review #1

Last week's progress

We have CAD'd most of the model for the project and ordered all the components we need. We finalized which components we wanted to go with, including picking which motors to use and deciding which components in Detkin we can use and which components we want to order. We have finalized the CAD design for the wheel and for the connectors between the frame and the rods. We have begun laser cutting and are planning on finishing assembly physically integrate our electronic components into the design next week. We still need to figure out how to add wheels to the chassis that the plate spins on and how to connect the rotary encoder to the follower wheel and shaftf, so those will be mechanical challenges we need to figure out next week.

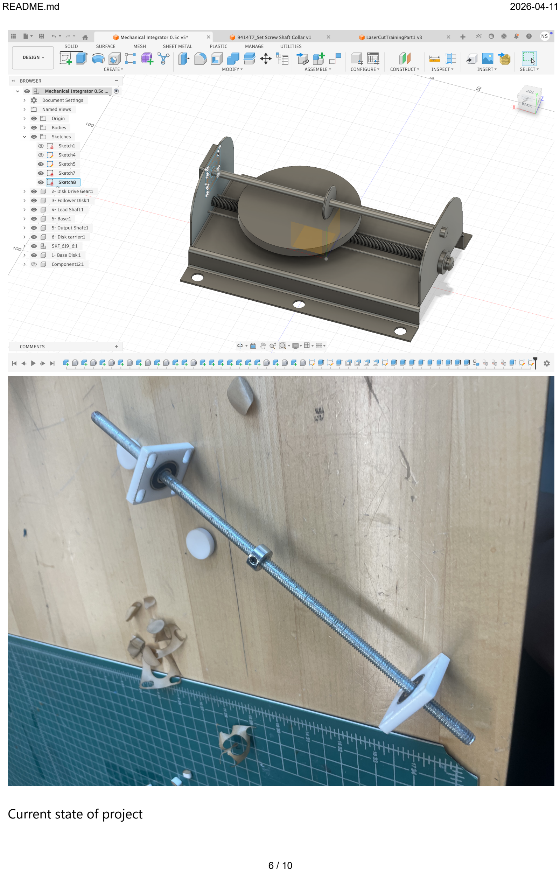
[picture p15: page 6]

Current state of project

We have a pretty solid foundation for this project. We understand how it works mechanically, which parts should be connected to one another, and how we want to integrate electronics. We have all parts purchsed, and at this point we just need to focus on finishing the mechanical parts and assembly as soon as possible so we can focus on hardware.
Next week's plan

Finishing printing and assembly, create a plan for how we are physically going to wire up our components, and create system diagrams for our code so we can integrate everything completely the week after.

Assignee Task

Estimated
time

Finished when...

Nevan | CAD and print the chassis | Two hours | The chassis is printed
Sebastian | Connector between rotary encoder and follower shaft wheel | Two hours | Connector is printed and glued to rotary encoder and shaft
Anjali | Connect follower wheel to shaft to bearings to rotary encoder | 1 hour | Entire top piece is connected
Nevan | CAD and print base | Two hours | Base is printed
Anjali | CAD and print wheels | Two hours | Wheels are printed and connected to chassis as well as track
Sebastian Final assembly | Two hours
| | | Connect all pieces together, motors are placed in correct location

## Sprint Review #2

Last week's progress

We completely finished CADing and have most of the parts printed! Most of our electronics have come in as well so we have begun to write code as well as assemble.


Current state of project

We have code for the rotary encoder that tells you the correct integral value, and most of the components assembled together, we just need the frame.

Next week's plan

Finishing coding is top priority, then work on assembly!

Assignee Task

Estimated
time

Finished when...

Nevan | print the frame | one hour | The frame is printed/ made sure all componenets are correct sizes/fit
Sebastian assemble the frame | two hours | mechanical frame is fully complete
Anjali | integrate electronics | 2 hour | all electronics are in the frame
Nevan | code the big stepper motor/y axis | five hours | the rod moves in tandem with the y axis of a function
Anjali | code the time/constant plate, integrate all code together | five hours | all code is complete
Sebastian final integration | five hours

Connect all pieces together, motors are placed in correct location, fully integrated together

## MVP Demo Final Report

Don't forget to make the GitHub pages public website! If you’ve never made a GitHub pages website before, you can follow this webpage (though, substitute your final project repository for the GitHub username one in the quickstart guide): https://docs.github.com/en/pages/quickstart
1. Video
2. Images
3. Results

### 3.1 Software Requirements Specification (SRS) Results

ID | Description | Validation Outcome

SRS-

01 | The IMU 3-axis acceleration will be measured with 16-bit depth every 100 milliseconds +/-10 milliseconds. | Confirmed, logged output from the MCU is saved to "validation" folder in GitHub repository.

### 3.2 Hardware Requirements Specification (HRS) Results

ID | Description | Validation Outcome

ID | Description | Validation Outcome

HRS-

01 | A distance sensor shall be used for obstacle detection. The sensor shall detect obstacles at a maximum distance of at least 10 cm. | Confirmed, sensed obstacles up to 15cm. Video in "validation" folder, shows tape measure and logged output to terminal.
4. Conclusion

## References

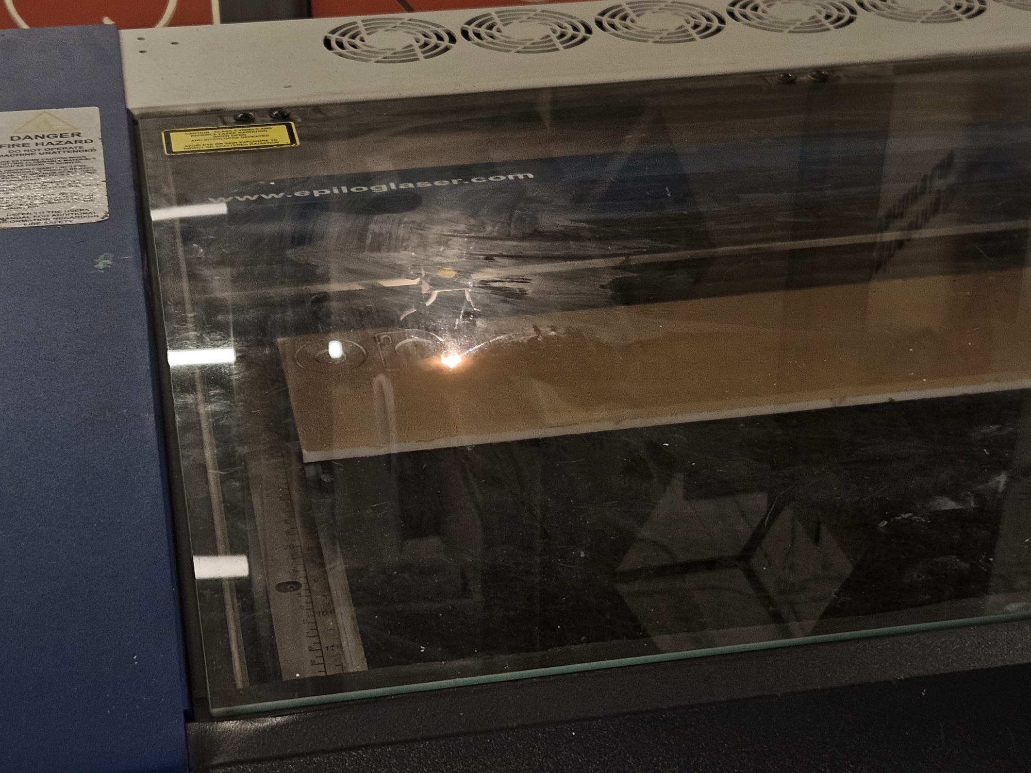
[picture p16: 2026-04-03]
images/lasercutter.jpg

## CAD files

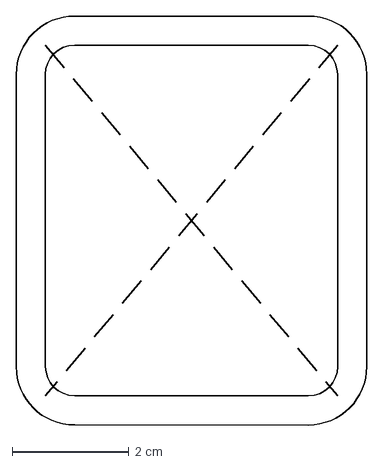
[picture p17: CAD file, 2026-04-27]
CAD models/other_holder.dxf
6.00 x 7.00 cm

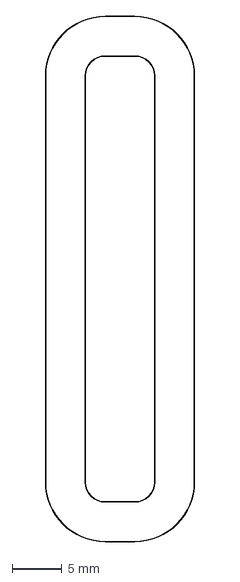
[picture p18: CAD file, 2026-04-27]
CAD models/small_slit_holder.dxf
15.0 x 53.0 mm

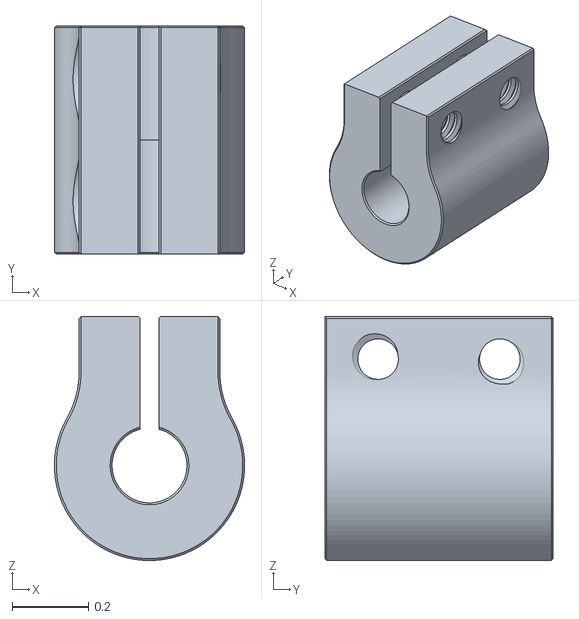
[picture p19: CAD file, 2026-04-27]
CAD models/stepper_motor_clamp.stl
0.5 x 0.6 x 0.641

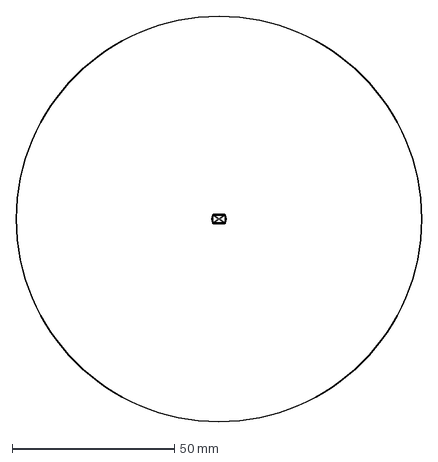
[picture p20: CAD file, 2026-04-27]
CAD models/base_plate.dxf
125.0 x 125.0 mm

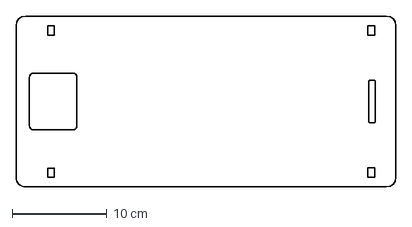
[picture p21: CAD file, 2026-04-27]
CAD models/base_plate_holed.dxf
40.0 x 18.0 cm

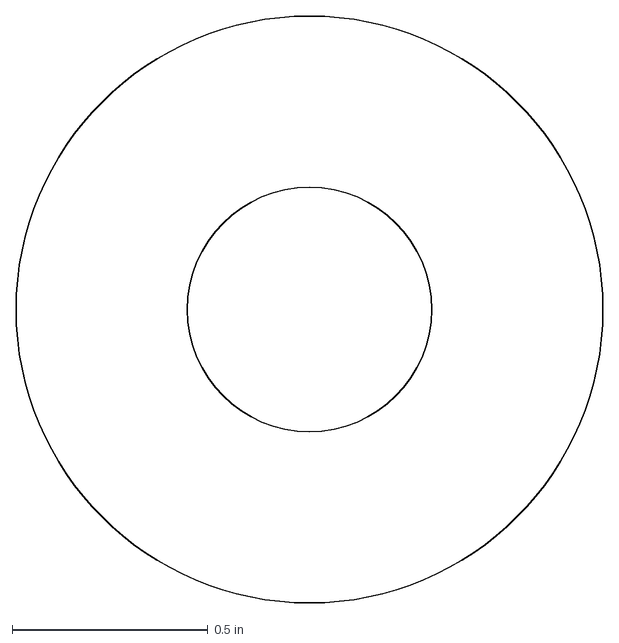
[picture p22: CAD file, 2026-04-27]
CAD models/follower_wheel.dxf
1.50 x 1.50 in

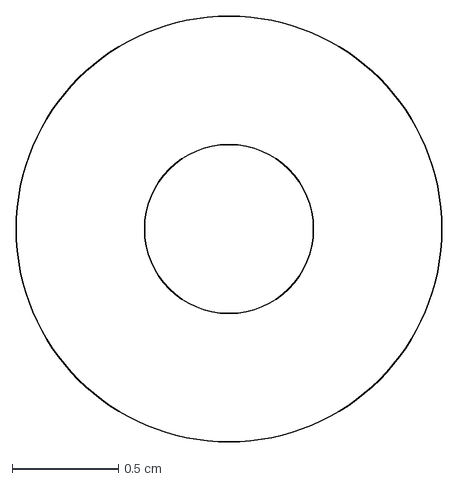
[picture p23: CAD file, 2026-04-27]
CAD models/wheel_integrated.dxf
2.00 x 2.00 cm

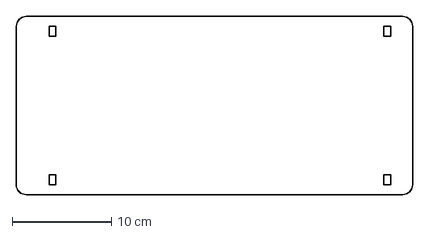
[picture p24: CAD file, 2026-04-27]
CAD models/base_plate_base_cm.dxf
40.0 x 18.0 cm

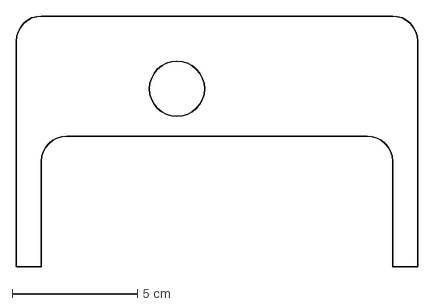
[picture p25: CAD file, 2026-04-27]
CAD models/vertical_frame.dxf
16.0 x 10.0 cm

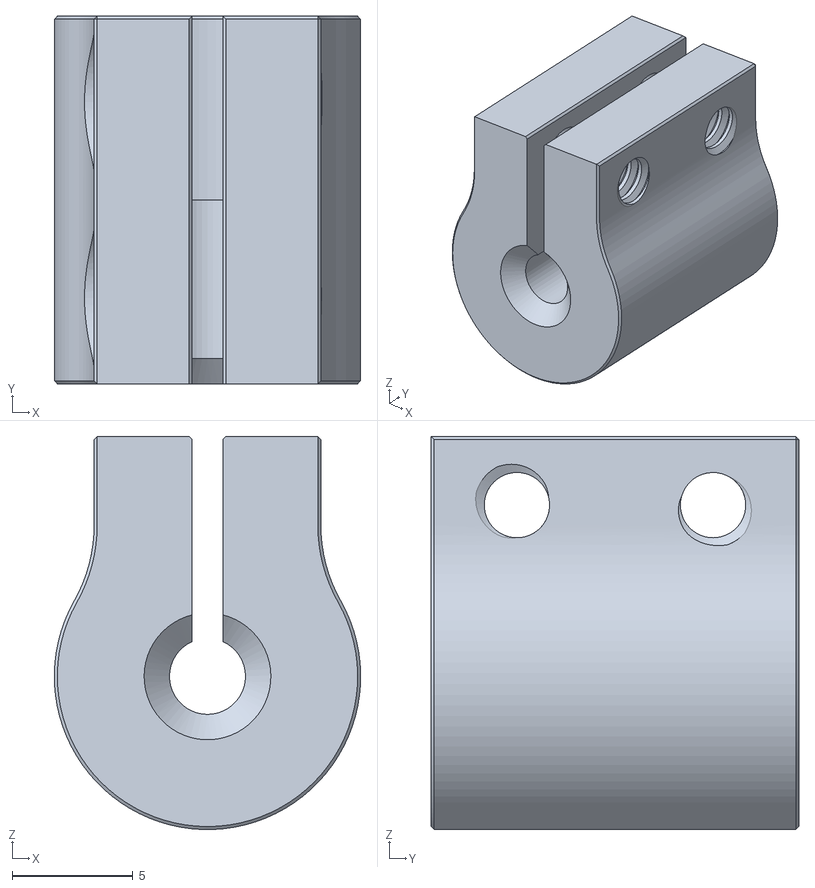
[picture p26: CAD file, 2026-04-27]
CAD models/encoder_clamp.stl
12.7 x 15.2 x 16.3

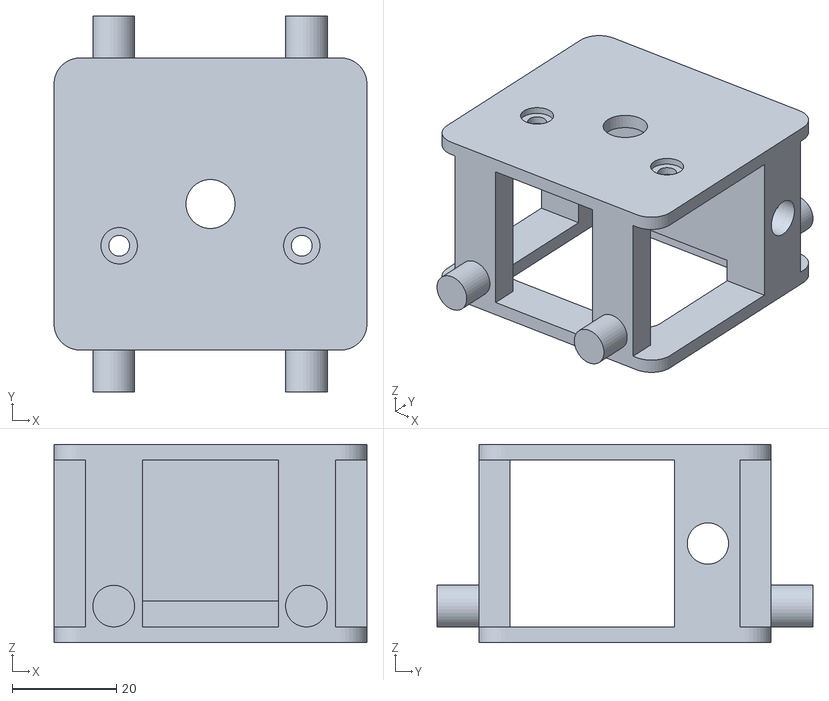
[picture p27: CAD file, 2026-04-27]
CAD models/chassis_platform.stl
60.0 x 72.0 x 38.0

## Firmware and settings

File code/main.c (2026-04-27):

/* 
 * File:   main.c
 * Author: sebastian
 *
 * Created on April 21, 2026, 4:50 AM
 */

#include <stdio.h>
#include <stdlib.h>
#include <avr/io.h>
#include "time.h"
#include "ASCII_LUT.h"
#include "LCD_GFX.h"
#include "ST7735.h"
#include "uart.h"
#include <avr/interrupt.h>

#define F_CPU 16000000UL

#include "util/delay.h"

/*
 * 
 */



#define CS_ENC PD7
#define ENABLE_BIG PC4

/*---global variables---*/

int16_t shared_integral = 0;
uint16_t shared_position = 0;
uint16_t global_ADC = 512;

/*---- init functions ----*/

//
void init_pwm_big_step (void){

    TCCR3B |= (1<<CS32)|(1<<WGM33);//WGM 3 2 and all CSx
    TCCR3A |= (1<<COM3B1)|(1<<WGM30); //COM3Ax COM3Bx WGM 1 0
    DDRD |= (1<<PD2);
    DDRC |= (1<<PC5)|(1<<PC4);
    PORTD |= (1<<PD2);
}

void init_pwm_little_step (void){
    TCCR2B |=(1<<CS22)|(1<<WGM22)(1<<CS21); 
    TCCR2A |=(1<<COM2B1)|(1<<WGM20);
    DDRD |= (1<<PD3); 
}

void init_interrupt_encoder(void){
    TCCR1B |= (1<<CS12)|(1<<CS10)|(1<<WGM12); // prescaler of 1024
    TIMSK1 |= (1<<OCIE1A);
	OCR1A = 255;
}

void init_LCD(void){
    
	lcd_init();
    LCD_setScreen(0xFFFF);
    LCD_drawLine(0,LCD_HEIGHT/2,LCD_WIDTH, LCD_HEIGHT/2, 0x0000);

}

void init_encoder(void){
    
    DDRD |= (1<<CS_ENC);
    SPCR1 = (1<<SPE1) | (1<<MSTR1) | (1<<SPR11);		//Enable SPI, Master, set clock rate much slower than initially set
	SPSR1 = (1<<SPI2X1);	
    DDRC |= (1<<PC1); // set clock as output
}

void init_slider(void){
    ADMUX |= (1<<MUX1)|(1<<REFS0);
    ADCSRA |= (1<<ADEN)|(1<<ADSC)|(1<<ADPS2)|(1<<ADPS1)|(1<<ADPS0)|(1<<ADATE);
}

/*---- helper functions ----*/

char SPI_MasterTransmit(char cData)
{
    /* Start transmission */
    SPDR1 = cData;
    /* Wait for transmission complete */
    while(!(SPSR1 & (1<<SPIF1)));

    return SPDR1;
}

uint16_t encoder_position(void) {
    uint8_t high, low;
    uint16_t full;

// pull down encoder CS
    PORTD &= ~(1<<CS_ENC);
    _delay_us(10); // Wait >500ns

// SPI transfer

    high = SPI_MasterTransmit(0x00);

    low = SPI_MasterTransmit(0x00);
    PORTD |= (1<<CS_ENC);


// release encoder CS back up

    
    full = (high<<8)|low;
    
    return (full>>6);
}

void itoa (int16_t num, char* string, int length){
    if(num<0){
        *string = '+';
        num = -num;
    }
    else *string = '-';
    
    for(int i = 0; i< length - 1; i++){
        int temp = num/10;
        temp = num - temp*10;
        
        *(string + length - 1 - i) = temp + 48;
        num/= 10;
    }
    *(string + length) = '\0';
}


uint16_t integral_calc_and_return_position(int16_t* integral, uint16_t prevposition){
    
       
    uint16_t position = encoder_position();
    
    int16_t limit = 2000;

    // calculate step size
    int16_t dx = position - prevposition;
    if (dx > 256) dx -= 512;    
    else if (dx < -256) dx += 512; 


    *integral += dx;
    //clamping the integral value
    if(*integral > limit) *integral = limit;
    if(*integral < -limit) *integral = -limit;
    // ready for next run
    return position;
    
}



int main(int argc, char** argv) {
    
    _delay_ms(5000);
	uart_init();
    init_pwm_big_step();
    init_pwm_little_step();
	_delay_ms(1000);
    init_LCD();
	_delay_ms(1000);
    init_encoder();
    init_interrupt_encoder();
    init_slider();
    
    
    // registers for big stepper
    OCR3A = 24;
    OCR3B = 12;
    
    
    //  registers for lil stepper
    OCR2A = 128;
    OCR2B = 64;
    
    /*--- variables for LCD ---*/
    int dx = 1; // step size of graphed integral
    uint8_t factor = 32;
    int count = LCD_WIDTH/dx; // number of steps required
    char buffer[10]; // buffer to keep track of integral value
    int prev = 60; //last value of integral
    shared_integral = 0; // current value of integral
    shared_position = encoder_position();
    
    sei();
    while(1){
        for(uint8_t i = 0; i< count; i++){
            
            
            // LCD transmission code
            itoa (shared_integral, buffer, 7);
            
            
            // perhaps have an array here to track and more easily erase, like an oscilloscope TODO
            int16_t temp = shared_integral;
            LCD_drawLine(i*dx,(prev/factor+LCD_HEIGHT/2),(i+1)*dx, (shared_integral/factor+LCD_HEIGHT/2), 0x0000);
            prev = temp;
            LCD_drawString(10, 20, buffer, 0x0000, 0xFFFF);
            
            
            _delay_ms(100);
            
            
        }
        // set LCD white? or have an array of the last few integrals and just always erase those? smarter and 
            shared_integral = 0;
        	prev = shared_integral;
			LCD_setScreen(0xFFFF);
            LCD_drawLine(0,LCD_HEIGHT/2,LCD_WIDTH, LCD_HEIGHT/2, 0x0000);


    }
    return (EXIT_SUCCESS);
}



ISR(TIMER1_COMPA_vect, ISR_BLOCK){
    shared_position = integral_calc_and_return_position(&shared_integral, shared_position);
    if(global_ADC != ADC){
        global_ADC = ADC;
        if(global_ADC<480){
            //direction change
           
            PORTC |=(1<<PC5);
            OCR3B = global_ADC/10 + 10;
            OCR3A = OCR3B*2;
            
        }
        else if(global_ADC>544){
          
            PORTC &= ~(1<<PC5);
            OCR3B = (1024 - global_ADC)/10 + 10;
            OCR3A = OCR3B*2;
        }
        else{
            OCR3B = 0;
        }
    }
}

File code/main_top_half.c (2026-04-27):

////////////////////////////////////////////////////////
////////////////////////////////////////////////////////
////    main.c
////////////////////////////////////////////////////////
////////////////////////////////////////////////////////

#define F_CPU 16000000UL

/*--------------------Libraries---------------------------*/
#include <stdlib.h>
#include <stdbool.h>
#include <string.h>
#include <stdio.h>

#include <avr/io.h>
#include <avr/sleep.h>


// CHANGE THE INCLUDES!!! for a new laptop


/* Scheduler include files. */
#include "AVR_FreeRTOS/FreeRTOS.h"
#include "AVR_FreeRTOS/task.h"
#include "AVR_FreeRTOS/queue.h"
#include "AVR_FreeRTOS/semphr.h"

/* util stuff */
#include "lib/uart.h"
#include "time.h"
#include "util/delay.h"



/* LCD stuff */
#include "lib2/ST7735.h"
#include "lib2/LCD_GFX.h"
#include "lib2/ASCII_LUT.h"


#define CS_ENC PD7

/*---global defines---*/

volatile int16_t shared_integral = 0;
SemaphoreHandle_t SPImutex;



/*----- HELPER Functions ------*/
void Initialise()
{
    
    // LCD STUFF
    ADMUX |= (1<<REFS0);

    DDRD |= (1<<CS_ENC);
    ADCSRA |= (1<<ADEN);
    ADCSRA |= (1<<ADSC);
	lcd_init();
    LCD_setScreen(0xFFFF);
    uart_init();
    DDRD |=(1<<PD0)|(1<<PD1)|(1<<PD2)|(1<<PD3);
    
    
    SPImutex = xSemaphoreCreateMutex();
    
    

}

// added inline to save stack budget
void inline _2_A()  { PORTD = (PORTD & 0xF0) | 0x01; } // 0001
void inline _2_AB() { PORTD = (PORTD & 0xF0) | 0x03; } // 0011
void inline _2_B()  { PORTD = (PORTD & 0xF0) | 0x02; } // 0010
void inline _2_BC() { PORTD = (PORTD & 0xF0) | 0x06; } // 0110
void inline _2_C()  { PORTD = (PORTD & 0xF0) | 0x04; } // 0100
void inline _2_CD() { PORTD = (PORTD & 0xF0) | 0x0C; } // 1100
void inline _2_D()  { PORTD = (PORTD & 0xF0) | 0x08; } // 1000
void inline _2_DA() { PORTD = (PORTD & 0xF0) | 0x09; } // 1001



/*------ SPI_ functions yoinked from reference manual example -----  */

//void SPI_MasterInit(void)
//{
///* Set MOSI and SCK output, all others input */
//DDR_SPI = (1<<DD_MOSI)|(1<<DD_SCK);
///* Enable SPI, Master, set clock rate fck/16  */
//SPCR0 = (1<<SPE)|(1<<MSTR)|(1<<SPR1)|(1<<CPHA);
//
//SPSR0 |= (1<<SPI2X);
//}

char SPI_MasterTransmit(char cData)
{
    /* Start transmission */
    SPDR0 = cData;
    /* Wait for transmission complete */
    while(!(SPSR0 & (1<<SPIF)));

    return SPDR0;
}



uint16_t encoder_position(void) {
    uint8_t high, low;
    uint16_t full;
    if (xSemaphoreTake(SPImutex, portMAX_DELAY) == pdTRUE) {
    // pull down encoder CS
        PORTD &= ~(1<<CS_ENC);
        _delay_us(10); // Wait >500ns
    
    // SPI transfer
    
        high = SPI_MasterTransmit(0x00);

        low = SPI_MasterTransmit(0x00);
        PORTD |= (1<<CS_ENC);
        
        xSemaphoreGive(SPImutex);
    }
    
    // release encoder CS back up
     
    
    full = (high<<8)|low;
    
    return (full>>6);
}

void itoa (int16_t num, char* string, int length){
    if(num<0){
        *string = '+';
        num = -num;
    }
    else *string = '-';
    
    for(int i = 0; i< length - 1; i++){
        int temp = num/10;
        temp = num - temp*10;
        
        *(string + length - 1 - i) = temp + 48;
        num/= 10;
    }
    *(string + length) = '\0';
}




/* TASKS*/

void taskEncoder(void *p){
    
    
    uint16_t prevposition = encoder_position();
    uint16_t position = 0;

    
    while(1){
                   /*---ENCODER LOGIC---*/
            
        position = encoder_position();
        
        // calculate step size
        int16_t dx = position - prevposition;
        if (dx > 256) dx -= 512;    
        else if (dx < -256) dx += 512; 

        taskENTER_CRITICAL();
        shared_integral += dx;
        //clamping the integral value
        if(shared_integral > 1500) shared_integral = 1500;
        if(shared_integral < -1500) shared_integral = -1500;
        taskEXIT_CRITICAL();
        // ready for next run
        prevposition = position; 


        vTaskDelay(pdMS_TO_TICKS(10));
    }
}

void taskEncoder2LCD(void *p) {



    int dx = 5;

    int count = LCD_WIDTH/dx;
    char buffer[10];
    int prev = 60;
    
    while(1){
        
        
        LCD_drawLine(0,LCD_HEIGHT/2,LCD_WIDTH, LCD_HEIGHT/2, 0x0000);
//          LCD_drawCircle(50, 50, 20, 0x0000);
        int track = 0;
        
        for(int i = 0; i< count; i++){
            
            
            

            // integral + absolute step
                    
              
            itoa (shared_integral, buffer, 7);
            
            
            
            /*----PRINTING----*/
//  
            
            if (xSemaphoreTake(SPImutex, portMAX_DELAY) == pdTRUE) {
                
            LCD_drawLine(i*dx,(prev/50+LCD_HEIGHT/2),(i+1)*dx, (shared_integral/50+LCD_HEIGHT/2), 0x0000);
            prev = shared_integral;
            
            LCD_drawString(10, 20, buffer, 0x0000, 0xFFFF);
            
            xSemaphoreGive(SPImutex);
            
            vTaskDelay(pdMS_TO_TICKS(50));


            }
            
//            printf("hello \n");
            
            
            
            
//            printf("%d \n", encoder_val);
            vTaskDelay(pdMS_TO_TICKS(50));
        }
        
        
        if (xSemaphoreTake(SPImutex, portMAX_DELAY) == pdTRUE) {

            LCD_setScreen(0xFFFF);
            
            xSemaphoreGive(SPImutex);
        }
        
        
        vTaskDelay(pdMS_TO_TICKS(10));
  
    
    }
    
    
}


void taskSteppersmall(void *p){
  
    while(1){
        
        
        _2_AB();
        
        vTaskDelay(pdMS_TO_TICKS(10));

        _2_BC();
        
        vTaskDelay(pdMS_TO_TICKS(10));

        _2_CD();
                
        vTaskDelay(pdMS_TO_TICKS(10));

        _2_DA();
        
        
        vTaskDelay(pdMS_TO_TICKS(10));
    }
    
}



int main(void) {
    
    
    Initialise();

    
    
    printf("hello world \n");
    
    xTaskCreate(taskEncoder2LCD, "tA", 256, NULL, 3, NULL);
    
//    xTaskCreate(taskSteppersmall, "tB", 128, NULL, 3, NULL);
    
    xTaskCreate(taskEncoder, "tC", 90, NULL, 2, NULL);
    
    

    vTaskStartScheduler();
    while(1);
}

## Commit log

2026-04-10 Add encoder functionality with SPI communication
2026-04-20 updates to motor stepper + button + joystick
2026-04-20 Main for rotory encoder display functionality
2026-04-26 Refactor PWM and encoder initialization settings
    Updated PWM initialization and interrupt handling for better performance. Adjusted limits and step sizes for encoder and LCD.
2026-04-27 uploading cad files, moving code to specific code file
    [base_plate.dxf, base_plate_base_cm.dxf, base_plate_holed.dxf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]
